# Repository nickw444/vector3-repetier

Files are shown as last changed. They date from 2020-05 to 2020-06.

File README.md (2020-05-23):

# Eaglemoss Vector 3 3D Printer Repetier Firmware Configuration

In this repository you will find:

* [Repetier Firmware configuration](repetier/Configuration.h) for this printer
* [Repetier Firmware patch](repetier/bluetooth-serial.diff) to enable IO on UART1 for a Bluetooth interface
* [Textual description of printer settings](Repetier-Host/printer-settings.md) for this printer within Repetier Host
* [Configuration for PrusaSlicer](PrusaSlicer/PrusaSlicer_config_bundle.ini)

This is not my own printer, but rather I spent some time configuring it for a friend.

## Resources used

* [smalcolmbrown/V3-Sprinter-Melzi_1_01](https://github.com/smalcolmbrown/V3-Sprinter-Melzi_1_01) firmware rewrite
* [Vector3 Wire List](https://v3uc.com/assets/Vector_3D_wire_list.pdf)
* [Vector3 User Community Forums](https://v3uc.com/)

## Why Repetier Firmware?

Good question... 3D printing is a very new world for me, having absolutely zero experience. When
I first began working with this printer, I was having consistent connection issues both during 
prints and during initial connection negotiation with the printer. I wanted to try alternative 
firmware to see if the firmware was the issue. 

My first attempt was to use [smalcolmbrown/V3-Sprinter-Melzi_1_01](https://github.com/smalcolmbrown/V3-Sprinter-Melzi_1_01) 
rewrite of the stock firmware. However, whilst using this firmware I continued to have intermittent 
connection issues both during printing and whilst connecting.

I looked around and compared different open source firmware's available. I considered the following:
 
* [RepRap Firmware](https://github.com/Duet3D/RepRapFirmware): Configuration tool didn't appear to
  support Sanguinololu out of the box.
* [Marlin Firmware](https://marlinfw.org/): Very complicated Configuration.h without an official 
  configuration tool
* [Repetier Firmware](https://www.repetier.com/documentation/repetier-firmware/): Less complex 
  Configuration.h albeit less documentation, however has an official configuration tool supporting 
  Sanguinololu out of the box.

Repetier was straightforward enough to configure and flash to my controller via USB.

## Issues I encountered along the way (and a tldr of the solution)

* Legacy bootloader meant I had to modify boards.txt to support slower bootloader baud rate:
    * Connect ISP programmer (Arduino Uno as ISP) and flash MightyCore as bootloader
* Inaccurate X/Y dimensions on prints
    * Check belts are tight (mine were loose)
    * Adjust X/Y steps per mm if confirmed that belts are tight and not slipping
* Unrecoverable timeouts during printing
    * Replace stock firmware with Repetier and add HC-06 Bluetooth serial

## Features

- [x] X/Y/Z End stops distance
- [x] X/Y/Z Speed & Acceleration
- [x] Thermister calibration
- [x] Heating element
- [x] Heading bed
- [x] Cooling fan control: https://v3uc.com/forums/topic/cooling-fan-issue-91/ - ensure switch 
      on extruder board is in correct position
- [x] PID temperature control for extruder, specifically I-gain to keep setpoint during printing

### Unsupported 

- [ ] Hood Switch: Not possible. controlled via i2c on the daughter board.
- [ ] Extruder LED: Not possible. controlled via i2c on the daughter board.
- [ ] Front button: Not possible. controlled via i2c on the daughter board.
- [ ] Front button LED: Not possible. controlled via i2c on the daughter board.

## Bed Adhesion Hacks

Bed adhesion is quite tricky on this machine (or perhaps my lack of 3D printing experience is to 
blame) here. However, I have found that I can improve bed adhesion with the following:

* Use masking tape to cover the bed
* Ensure bed is completely flat (duh) and printer height correctly set
* Slow down first layer when printing - 20mm/s first layer speed seems to help
* Prime the extruder prior to printing using custom G-code

### Filament Start G-code

```
G1 E15 F100 ; prime/extrude 15mm into dump area
G92 E0 ; reset extruder
```

### Printer Start G-code

```
G28 ; home all axes
G1 X140 Y0 Z2 F5000 ; lift nozzle 2mm and go to dump area
```

Pre-configured PrusaSlicer configuration can be found in the [PrusaSlicer](PrusaSlicer) directory.

### Things I Did

* Attempted re-flash of [unofficial upgrade of stock FW](https://github.com/smalcolmbrown/V3-Sprinter-Melzi_1_01)
    * Experiencing drop out and pausing during printing
    * Annoying to re-flash as have to use an old version of Arduino
    * Managed to calibrate X/Y/Z axis
        * In retrospect this calibration was unnecessary, the underlying issue was loose belts
* Attempted re-flash of [Repetier-FW](https://www.repetier.com/documentation/repetier-firmware/)
    * Compiled using Arduino V1.8.12 against [Sanguino](https://github.com/Lauszus/Sanguino), makes dev loop easier for tweaking
    * Due to legacy bootloader, have to manually change boards.txt to support firmware flash at 57600 baud.
    * Slightly better in terms of reliability. 
    * Still experiencing drop outs and pausing during printing
    * Flaky connection, does not connect with my Macbook Pro
    * Adjusted baud to 57600 with no success
* Upgraded bootloader to [MightyCore](https://github.com/MCUdude/MightyCore), re-flashed with Arduino UNO as ISP Programmer
    * Brown out detection @ 4.7V (guess)
    * 16MHZ External Clock
    * Sanguino Pinout
    * Can now flash without legacy baud change in boards.txt
* Compiled Repetier against [MightyCore](https://github.com/MCUdude/MightyCore) (instead of [Sanguino](https://github.com/Lauszus/Sanguino))
    * Drop outs seem to have decreased.
    * Initiating a connection is near instant
    * Macbook Pro able to connect immediately
* Re-flashed bootloader and disabled BOD to ensure this was not contributing to drop-outs.
    * Drop outs still occurring.
* Disable firmware watchdog timer
    * Drop outs still occurring.
* Re-built printer
    * Removed unused daughter board to front power LED + button
        * Might try to figure out how to add an I2C display + connect buttons directly to main board.
    * Improved internal cable management, moving USB cable away from power
    * Tightened belts on X/Y axis. Y axis was loose, no wonder it needed adjustment. 
* Print dry-run x3 15 minute prints without dropped connection, but still occasional dropout being encountered
    * Might be good enough? Long prints probably won't be possible.
    * Power quality issue in our apartment building? Florescent lights on the same circuit?
* Modify firmware and connect via Bluetooth
    * See [repetier/bluetooth-serial.diff](repetier/bluetooth-serial.diff) for patch applied to 
      Repetier 1.0.3. [Source](https://forum.repetier.com/discussion/5317/second-uart-for-bluetooth-isnt-working-after-upgrade-from-0-9-2-to-1-0-1)
    * Recompiled
        * Re-enabled watchdog
    * Bluetooth connection appears more reliable than USB for printing

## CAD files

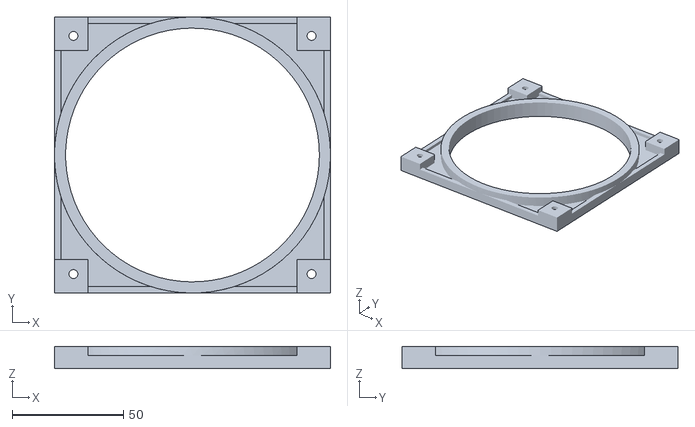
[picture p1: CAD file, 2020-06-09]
projects/cpu_fan_bracket_full.stl
124.0 x 124.0 x 10.0

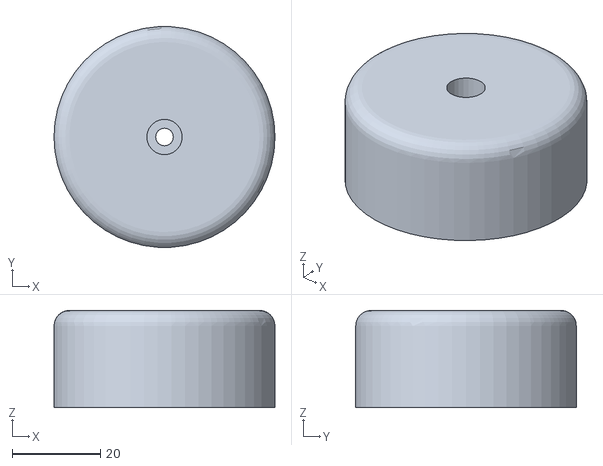
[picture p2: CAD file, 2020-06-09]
projects/pc_case_feet_front.stl
50.0 x 49.9 x 22.0

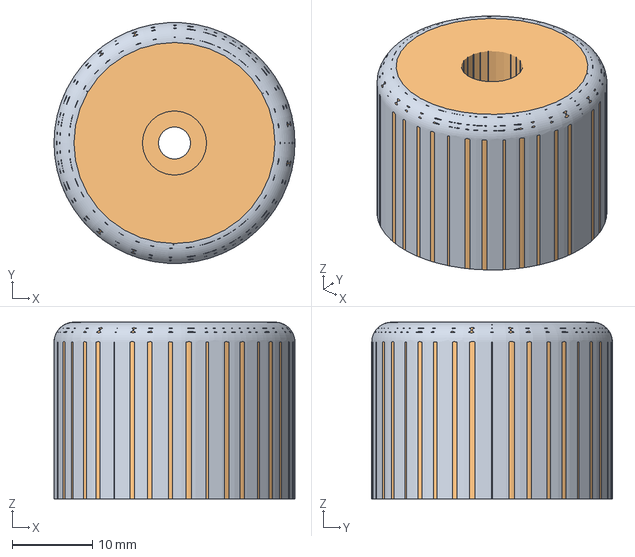
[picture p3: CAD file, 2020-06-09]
projects/pc_case_feet.FCStd
30.0 x 30.0 x 22.0 mm
Rear
Rear (Meshed)

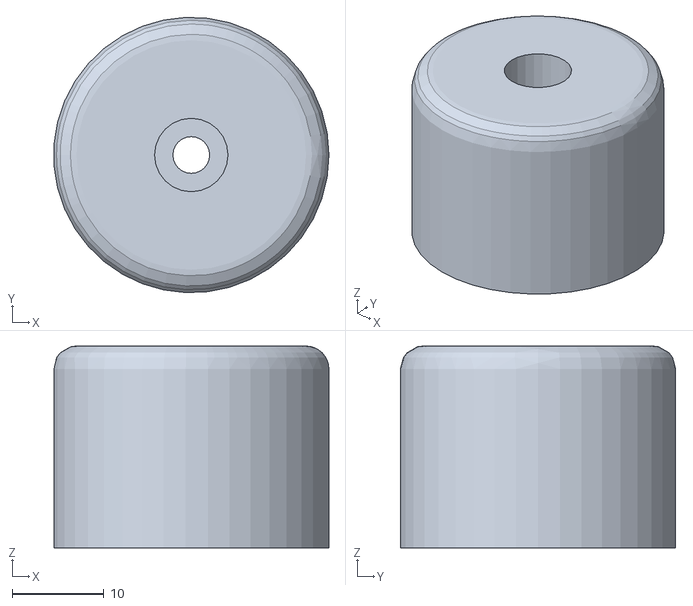
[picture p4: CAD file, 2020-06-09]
projects/pc_case_feet_rear.stl
30.0 x 30.0 x 22.0

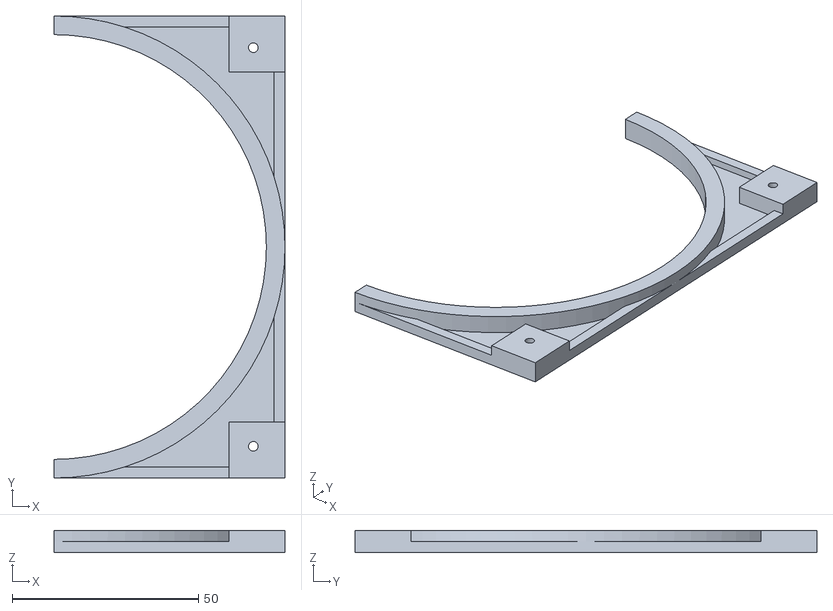
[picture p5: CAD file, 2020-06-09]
projects/cpu_fan_bracket_half.stl
62.0 x 124.0 x 6.00

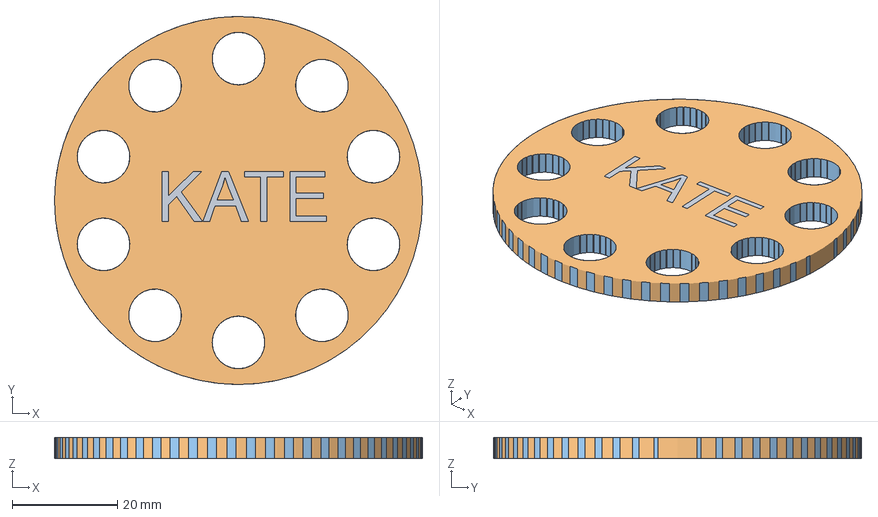
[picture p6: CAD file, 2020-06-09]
projects/thread_holder.FCStd
70.0 x 70.0 x 4.00 mm
Cut (Meshed)

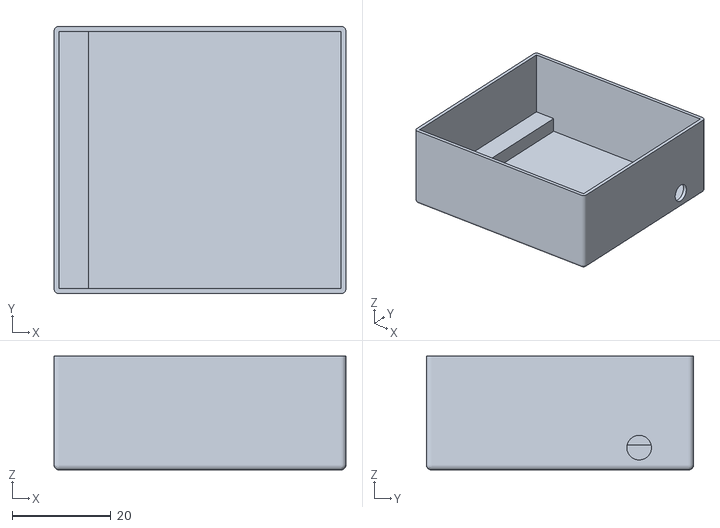
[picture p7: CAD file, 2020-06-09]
projects/blind_tx_433_case_base.stl
59.0 x 54.0 x 23.0

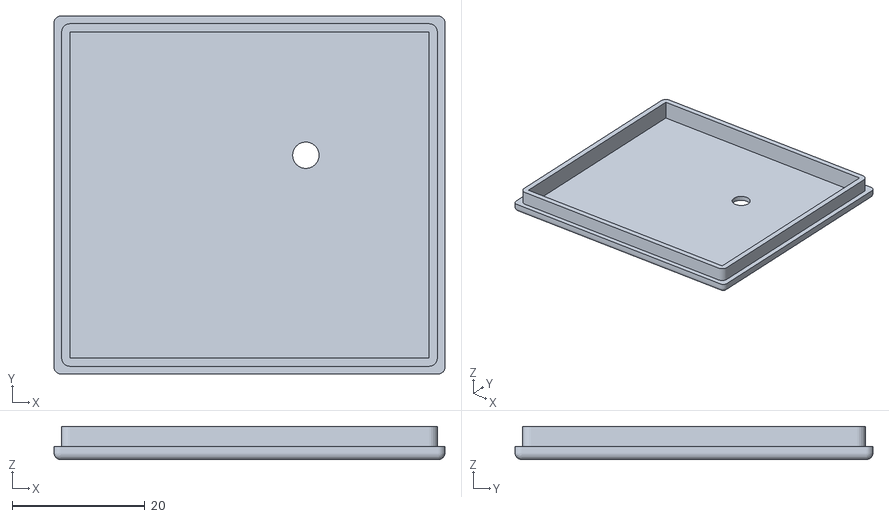
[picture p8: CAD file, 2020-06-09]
projects/blind_tx_433_case_lid.stl
59.0 x 54.0 x 5.00

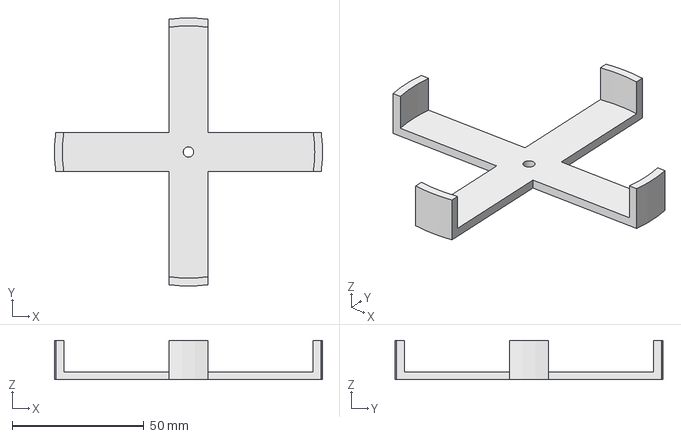
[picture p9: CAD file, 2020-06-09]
projects/jar_thermometer_holder.FCStd
101.9 x 101.9 x 15.0 mm

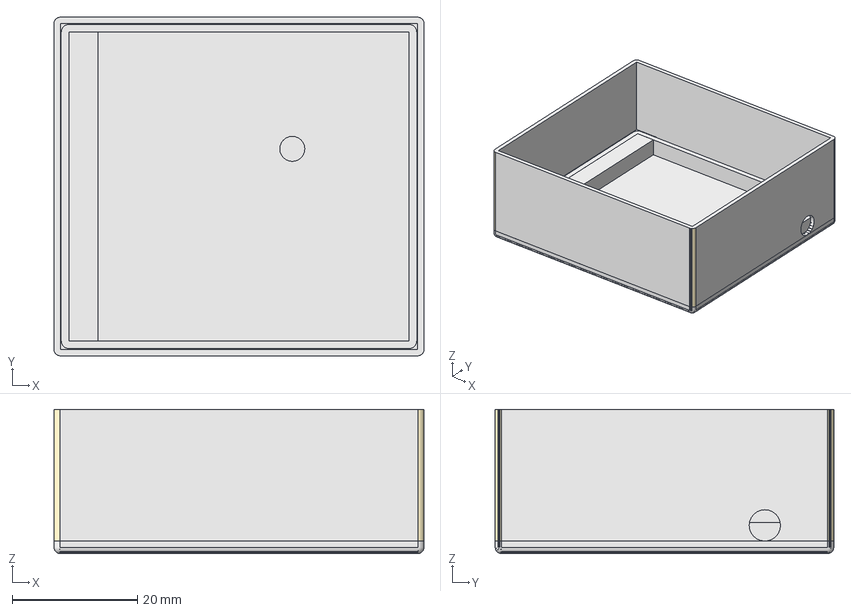
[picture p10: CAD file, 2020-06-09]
projects/blind_tx_433_case.FCStd
59.0 x 54.0 x 23.0 mm
Base
Lid
Base (Meshed)
Lid (Meshed)

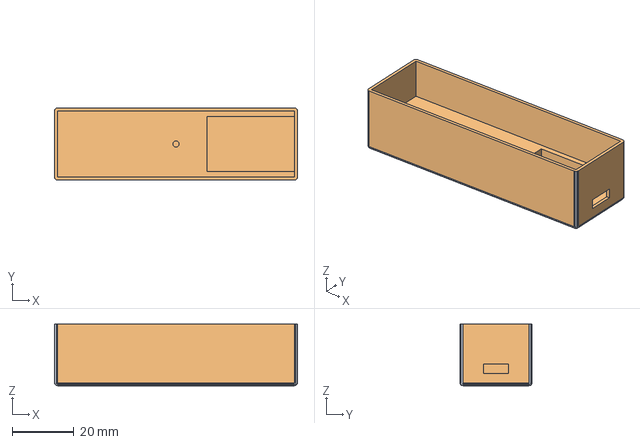
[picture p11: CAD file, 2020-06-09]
projects/18650_charger_case.FCStd
79.0 x 23.5 x 20.0 mm
Pocket002 (Meshed)

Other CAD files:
projects/cpu_fan_bracket.FCStd
projects/18650_charger_case.stl
projects/jar_thermometer_holder.stl
projects/thread_holder.stl

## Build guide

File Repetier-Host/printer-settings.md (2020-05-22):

## Connection

| Setting | Value |
|---|---|
| Baud Rate | 115200 |

## Behaviour

| Setting | Value |
|---|---|
| Travel Feedrate | 4800 mm/min |
| Z Axis Travel Feedrate | |
| Default Extruder Temperature | 180 C |
| Default heated bed temperature | 55 C |
| Number of Extruder | 1 |
| Check extruder & heated bed every | 1 seconds |
| Don't log temperature request (M105) | checked |
| Dump area position | X = 142, Y = 0, Z-min = 0 |
| Go to dispose after job/job kill | checked |
| Disable extruder after job/job kill | checked |
| Disable heated bed after job/job kill | checked |
| Disable motors after job/job kill | unchecked |
| Add to comp. printing time | 0% | 

## Dimension

| Setting | Value |
|---|---|
| Home X | x min |
| Home Y | y min |
| Home Z | z max |
| X Min | 0 |
| Y Min | 0 |
| X Max | 142 |
| Y Max | 110 |
| Printer type | Classic Printer |
| Print Area Width | 135 mm |
| Print Area Depth | 110 mm |
| Print Area Height | 126.0 mm | 
| Bed Front | 0 mm |
| Bed Left | 0 mm |

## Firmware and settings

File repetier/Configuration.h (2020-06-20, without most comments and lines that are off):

#define CONFIGURATION_H
#define NUM_EXTRUDER 1
#define MOTHERBOARD 62
#include "pins.h"
#undef FAN_PIN
#define FAN_PIN 4
#undef FAN_BOARD_PIN
#define FAN_BOARD_PIN -1
#define BOARD_FAN_SPEED 255
#define BOARD_FAN_MIN_SPEED 0
#define FAN_THERMO_PIN -1
#define FAN_THERMO_MIN_PWM 128
#define FAN_THERMO_MAX_PWM 255
#define FAN_THERMO_MIN_TEMP 45
#define FAN_THERMO_MAX_TEMP 60
#define FAN_THERMO_THERMISTOR_PIN -1
#define FAN_THERMO_THERMISTOR_TYPE 1
#undef Z_MIN_PIN
#define Z_MIN_PIN -1
#undef Z_MAX_PIN
#define Z_MAX_PIN ORIG_Z_MIN_PIN
#define BLUETOOTH_SERIAL 1
#define BLUETOOTH_BAUD  115200
#define MIXING_EXTRUDER 0
#define DRIVE_SYSTEM 0
#define XAXIS_STEPS_PER_MM 78.82
#define YAXIS_STEPS_PER_MM 78.82
#define ZAXIS_STEPS_PER_MM 2560
#define EXTRUDER_FAN_COOL_TEMP 50
#define PDM_FOR_EXTRUDER 0
#define PDM_FOR_COOLER 0
#define DECOUPLING_TEST_MAX_HOLD_VARIANCE 20
#define DECOUPLING_TEST_MIN_TEMP_RISE 1
#define KILL_IF_SENSOR_DEFECT 0
#define RETRACT_ON_PAUSE 2
#define PAUSE_START_COMMANDS ""
#define PAUSE_END_COMMANDS ""
#define SHARED_EXTRUDER_HEATER 0
#define EXT0_X_OFFSET 0
#define EXT0_Y_OFFSET 0
#define EXT0_Z_OFFSET 0
#define EXT0_STEPS_PER_MM 99.615
#define EXT0_TEMPSENSOR_TYPE 5
#define EXT0_TEMPSENSOR_PIN TEMP_0_PIN
#define EXT0_HEATER_PIN HEATER_0_PIN
#define EXT0_STEP_PIN ORIG_E0_STEP_PIN
#define EXT0_DIR_PIN ORIG_E0_DIR_PIN
#define EXT0_INVERSE 1
#define EXT0_ENABLE_PIN ORIG_E0_ENABLE_PIN
#define EXT0_ENABLE_ON 0
#define EXT0_MIRROR_STEPPER 0
#define EXT0_STEP2_PIN ORIG_E0_STEP_PIN
#define EXT0_DIR2_PIN ORIG_E0_DIR_PIN
#define EXT0_INVERSE2 0
#define EXT0_ENABLE2_PIN ORIG_E0_ENABLE_PIN
#define EXT0_MAX_FEEDRATE 50
#define EXT0_MAX_START_FEEDRATE 20
#define EXT0_MAX_ACCELERATION 5000
#define EXT0_HEAT_MANAGER 1
#define EXT0_PREHEAT_TEMP 190
#define EXT0_WATCHPERIOD 1
#define EXT0_PID_INTEGRAL_DRIVE_MAX 100
#define EXT0_PID_INTEGRAL_DRIVE_MIN 40
#define EXT0_PID_PGAIN_OR_DEAD_TIME 3.49
#define EXT0_PID_I 0.09
#define EXT0_PID_D 32.73
#define EXT0_PID_MAX 200
#define EXT0_ADVANCE_K 0
#define EXT0_ADVANCE_L 0
#define EXT0_ADVANCE_BACKLASH_STEPS 0
#define EXT0_WAIT_RETRACT_TEMP 150
#define EXT0_WAIT_RETRACT_UNITS 0
#define EXT0_SELECT_COMMANDS ""
#define EXT0_DESELECT_COMMANDS ""
#define EXT0_EXTRUDER_COOLER_PIN -1
#define EXT0_EXTRUDER_COOLER_SPEED 255
#define EXT0_DECOUPLE_TEST_PERIOD 30000
#define EXT0_JAM_PIN -1
#define EXT0_JAM_PULLUP 0
#define FEATURE_RETRACTION 1
#define AUTORETRACT_ENABLED 0
#define RETRACTION_LENGTH 3
#define RETRACTION_LONG_LENGTH 13
#define RETRACTION_SPEED 40
#define RETRACTION_Z_LIFT 0
#define RETRACTION_UNDO_EXTRA_LENGTH 0
#define RETRACTION_UNDO_EXTRA_LONG_LENGTH 0
#define RETRACTION_UNDO_SPEED 20
#define FILAMENTCHANGE_X_POS 0
#define FILAMENTCHANGE_Y_POS 0
#define FILAMENTCHANGE_Z_ADD  2
#define FILAMENTCHANGE_REHOME 1
#define FILAMENTCHANGE_SHORTRETRACT 5
#define FILAMENTCHANGE_LONGRETRACT 50
#define JAM_METHOD 1
#define JAM_STEPS 220
#define JAM_SLOWDOWN_STEPS 320
#define JAM_SLOWDOWN_TO 70
#define JAM_ERROR_STEPS 500
#define JAM_MIN_STEPS 10
#define JAM_ACTION 0
#define RETRACT_DURING_HEATUP true
#define PID_CONTROL_RANGE 20
#define SKIP_M109_IF_WITHIN 2
#define SCALE_PID_TO_MAX 0
#define TEMP_HYSTERESIS 0
#define EXTRUDE_MAXLENGTH 160
#define NUM_TEMPS_USERTHERMISTOR0 100
#define USER_THERMISTORTABLE0 { \
    { 1 * 4 , 500 * 8 }, \
    { 12 * 4 , 300 * 8 }, \
    { 14 * 4 , 288 * 8 }, \
    { 23 * 4 , 254 * 8 }, \
    { 31 * 4 , 234 * 8 }, \
    { 40 * 4 , 220 * 8 }, \
    { 66 * 4 , 192 * 8 }, \
    { 80 * 4 , 182 * 8 }, \
    { 92 * 4 , 175 * 8 }, \
    { 109 * 4 , 167 * 8 }, \
    { 120 * 4 , 162 * 8 }, \
    { 124 * 4 , 160 * 8 }, \
    { 131 * 4 , 157 * 8 }, \
    { 142 * 4 , 153 * 8 }, \
    { 147 * 4 , 151 * 8 }, \
    { 156 * 4 , 148 * 8 }, \
    { 163 * 4 , 146 * 8 }, \
    { 181 * 4 , 141 * 8 }, \
    { 196 * 4 , 137 * 8 }, \
    { 218 * 4 , 132 * 8 }, \
    { 278 * 4 , 120 * 8 }, \
    { 295 * 4 , 117 * 8 }, \
    { 307 * 4 , 115 * 8 }, \
    { 319 * 4 , 113 * 8 }, \
    { 325 * 4 , 112 * 8 }, \
    { 338 * 4 , 110 * 8 }, \
    { 345 * 4 , 109 * 8 }, \
    { 352 * 4 , 108 * 8 }, \
    { 359 * 4 , 107 * 8 }, \
    { 366 * 4 , 106 * 8 }, \
    { 373 * 4 , 105 * 8 }, \
    { 380 * 4 , 104 * 8 }, \
    { 387 * 4 , 103 * 8 }, \
    { 394 * 4 , 102 * 8 }, \
    { 401 * 4 , 101 * 8 }, \
    { 409 * 4 , 100 * 8 }, \
    { 416 * 4 , 99 * 8 }, \
    { 424 * 4 , 98 * 8 }, \
    { 432 * 4 , 97 * 8 }, \
    { 439 * 4 , 96 * 8 }, \
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
}
#define NUM_TEMPS_USERTHERMISTOR1 0
#define USER_THERMISTORTABLE1 {}
#define NUM_TEMPS_USERTHERMISTOR2 0
#define USER_THERMISTORTABLE2 {}
#define GENERIC_THERM_VREF 5
#define GENERIC_THERM_NUM_ENTRIES 33
#define HEATER_PWM_SPEED 0
#define COOLER_PWM_SPEED 0
#define HAVE_HEATED_BED 1
#define HEATED_BED_PREHEAT_TEMP 55
#define HEATED_BED_MAX_TEMP 120
#define SKIP_M190_IF_WITHIN 3
#define HEATED_BED_SENSOR_TYPE 5
#define HEATED_BED_SENSOR_PIN TEMP_1_PIN
#define HEATED_BED_HEATER_PIN HEATER_1_PIN
#define HEATED_BED_SET_INTERVAL 5000
#define HEATED_BED_HEAT_MANAGER 0
#define HEATED_BED_PID_INTEGRAL_DRIVE_MAX 255
#define HEATED_BED_PID_INTEGRAL_DRIVE_MIN 80
#define HEATED_BED_PID_PGAIN_OR_DEAD_TIME   196
#define HEATED_BED_PID_IGAIN   33
#define HEATED_BED_PID_DGAIN 290
#define HEATED_BED_PID_MAX 255
#define HEATED_BED_DECOUPLE_TEST_PERIOD 300000
#define MIN_EXTRUDER_TEMP 150
#define MAXTEMP 275
#define MIN_DEFECT_TEMPERATURE -10
#define MAX_DEFECT_TEMPERATURE 290
#define MILLISECONDS_PREHEAT_TIME 30000
#define SUPPORT_LASER 0
#define LASER_PIN -1
#define LASER_ON_HIGH 1
#define LASER_WARMUP_TIME 0
#define LASER_PWM_MAX 255
#define LASER_WATT 2
#define SUPPORT_CNC 0
#define CNC_WAIT_ON_ENABLE 300
#define CNC_WAIT_ON_DISABLE 0
#define CNC_ENABLE_PIN -1
#define CNC_ENABLE_WITH 1
#define CNC_DIRECTION_PIN -1
#define CNC_DIRECTION_CW 1
#define CNC_PWM_MAX 255
#define CNC_RPM_MAX 8000
#define CNC_SAFE_Z 150
#define DEFAULT_PRINTER_MODE 0
#define MULTI_ZENDSTOP_HOMING 0
#define ENDSTOP_PULLUP_X_MIN true
#define ENDSTOP_X_MIN_INVERTING true
#define MIN_HARDWARE_ENDSTOP_X true
#define ENDSTOP_PULLUP_Y_MIN true
#define ENDSTOP_Y_MIN_INVERTING true
#define MIN_HARDWARE_ENDSTOP_Y true
#define ENDSTOP_PULLUP_Z_MIN true
#define ENDSTOP_Z_MIN_INVERTING false
#define MIN_HARDWARE_ENDSTOP_Z false
#define ENDSTOP_PULLUP_Z2_MINMAX true
#define ENDSTOP_Z2_MINMAX_INVERTING false
#define MINMAX_HARDWARE_ENDSTOP_Z2 false
#define ENDSTOP_PULLUP_X_MAX true
#define ENDSTOP_X_MAX_INVERTING false
#define MAX_HARDWARE_ENDSTOP_X false
#define ENDSTOP_PULLUP_Y_MAX true
#define ENDSTOP_Y_MAX_INVERTING false
#define MAX_HARDWARE_ENDSTOP_Y false
#define ENDSTOP_PULLUP_Z_MAX true
#define ENDSTOP_Z_MAX_INVERTING true
#define MAX_HARDWARE_ENDSTOP_Z true
#define ENDSTOP_PULLUP_X2_MIN true
#define ENDSTOP_PULLUP_Y2_MIN true
#define ENDSTOP_PULLUP_Z2_MINMAX true
#define ENDSTOP_PULLUP_X2_MAX true
#define ENDSTOP_PULLUP_Y2_MAX true
#define ENDSTOP_X2_MIN_INVERTING false
#define ENDSTOP_Y2_MIN_INVERTING false
#define ENDSTOP_X2_MAX_INVERTING false
#define ENDSTOP_Y2_MAX_INVERTING false
#define MIN_HARDWARE_ENDSTOP_X2 false
#define MIN_HARDWARE_ENDSTOP_Y2 false
#define MAX_HARDWARE_ENDSTOP_X2 false
#define MAX_HARDWARE_ENDSTOP_Y2 false
#define X2_MIN_PIN -1
#define X2_MAX_PIN -1
#define Y2_MIN_PIN -1
#define Y2_MAX_PIN -1
#define Z2_MINMAX_PIN -1
#define max_software_endstop_r true
#define min_software_endstop_x false
#define min_software_endstop_y false
#define min_software_endstop_z false
#define max_software_endstop_x true
#define max_software_endstop_y true
#define max_software_endstop_z true
#define DOOR_PIN -1
#define DOOR_PULLUP 1
#define DOOR_INVERTING 0
#define ENDSTOP_X_BACK_MOVE 5
#define ENDSTOP_Y_BACK_MOVE 5
#define ENDSTOP_Z_BACK_MOVE 2
#define ENDSTOP_X_RETEST_REDUCTION_FACTOR 3
#define ENDSTOP_Y_RETEST_REDUCTION_FACTOR 3
#define ENDSTOP_Z_RETEST_REDUCTION_FACTOR 3
#define ENDSTOP_X_BACK_ON_HOME 7
#define ENDSTOP_Y_BACK_ON_HOME 15
#define ENDSTOP_Z_BACK_ON_HOME 0
#define ALWAYS_CHECK_ENDSTOPS 1
#define MOVE_X_WHEN_HOMED 0
#define MOVE_Y_WHEN_HOMED 0
#define MOVE_Z_WHEN_HOMED 0
#define X_ENABLE_ON 0
#define Y_ENABLE_ON 0
#define Z_ENABLE_ON 0
#define DISABLE_X 0
#define DISABLE_Y 0
#define DISABLE_Z 0
#define DISABLE_E 0
#define INVERT_X_DIR 0
#define INVERT_X2_DIR 0
#define INVERT_Y_DIR 0
#define INVERT_Y2_DIR 0
#define INVERT_Z_DIR 0
#define INVERT_Z2_DIR 0
#define INVERT_Z3_DIR 0
#define INVERT_Z4_DIR 0
#define X_HOME_DIR -1
#define Y_HOME_DIR -1
#define Z_HOME_DIR 1
#define X_MAX_LENGTH 142
#define Y_MAX_LENGTH 110
#define Z_MAX_LENGTH 126.0
#define X_MIN_POS 0
#define Y_MIN_POS 0
#define Z_MIN_POS 0
#define PARK_POSITION_X 0
#define PARK_POSITION_Y 0
#define PARK_POSITION_Z_RAISE 10
#define DISTORTION_CORRECTION 0
#define DISTORTION_CORRECTION_POINTS 5
#define DISTORTION_LIMIT_TO 2
#define DISTORTION_CORRECTION_R 100
#define DISTORTION_PERMANENT 1
#define DISTORTION_UPDATE_FREQUENCY 15
#define DISTORTION_START_DEGRADE 0.5
#define DISTORTION_END_HEIGHT 1
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

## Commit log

2020-05-11 Initial config
    [Configuration.h]
2020-05-11 Adjust bed size and z direction
    [Configuration.h]
2020-05-11 Reset EEPROM, invert Z
    [Configuration.h]
2020-05-11 Set z/y max length
    [Configuration.h]
2020-05-12 Tune endstops
    [Configuration.h]
2020-05-12 Adjust X/Y/Z feedrate/acceleration to stock firmware values
    [Configuration.h]
2020-05-12 Enable PWM Controlled extruder fan
    [Configuration.h]
2020-05-12 Enable watchdog
    [Configuration.h]
2020-05-12 No door endstop
    [Configuration.h]
2020-05-12 Add config for heated bed
    [Configuration.h]
2020-05-13 User defined thermistor table
    [Configuration.h]
2020-05-15 PID tuning for extruder
    [Configuration.h]
2020-05-16 Use max endstop for Z axis
    [Configuration.h]
2020-05-16 Move configuration to repetier dir + update steps per mm + max length
    [Configuration.h]
2020-05-16 Add Marlin configuration
    [Configuration.h, Configuration_adv.h]
2020-05-22 Remove generated config json blob
    [Configuration.h]
2020-05-22 Swap extruder fan with print cooling fan
    [Configuration.h]
2020-05-22 Fix indentation
    [Configuration.h]
2020-05-22 Increase X max length for dump area
    [Configuration.h]
2020-05-22 Increase decoupled heater test duration
    [Configuration.h]
2020-05-22 Remove marlin configuration
    [Configuration.h, Configuration_adv.h]
2020-05-22 Add repetier host printer settings
2020-05-23 Enable bluetooth serial communication + patch to solve bug in https://github.com/repetier/Repetier-Firmware/issues/799
    [Configuration.h]
2020-05-23 bed adhesion
2020-06-09 Add freecad projects + STLs
    [18650_charger_case.FCStd, 18650_charger_case.stl, blind_tx_433_case.FCStd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]
2020-06-09 Add pc case feet
    [pc_case_feet.FCStd, pc_case_feet_front.stl, pc_case_feet_rear.stl]
2020-06-20 EEPROM defaults
    [Configuration.h]

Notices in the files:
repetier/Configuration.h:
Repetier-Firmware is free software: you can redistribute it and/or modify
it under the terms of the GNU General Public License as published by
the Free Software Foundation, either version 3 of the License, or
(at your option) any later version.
